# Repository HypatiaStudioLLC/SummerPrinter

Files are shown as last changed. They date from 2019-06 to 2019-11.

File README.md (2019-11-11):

# SummerPrinter

Here you will find information about our 3D printer design.  This 3D printer was developed for our Build Your Own 3D Printer summer camps, which we ran in the summer of 2019 in Boulder, Colorado, USA.  At present we have 3D model files for all the 3D printed components of the printer, basic documentation, a bill of materials, and firmware configurations for Marlin.  More information is to come, and updates to the design as we improve it!

Our goals for this printer are, in no particular order, that this printer should:
* Print quickly and with high quality (not necessarily at the same time)
* Be compact and portable
* Be able to be assembled and commissioned by a teenager -- under supervision -- in a week-long half-day summer camp
* Print the three common materials (PLA, PETG, ABS)
* Have low cost
* Use standard components as much as possible to enable expansion and experimentation

(One motivation behind these goals was that, if we turned out to not get sign-ups for the camp, I wanted printer kits that I would be happy to assemble and use myself in our other classes.  Thus we would need to carry these printers into classrooms or community centers and use them without much setup, and we would use them to quickly print small objects that students design during a workshop or class.)

These goals led to the following design decisions:
* The printer uses a cartesian (Makerbot-style) motion system.  A Prusa-style motion system has limited acceleration due to the need to move the build plate and print horizontally.  CoreXY and delta motion systems support fast printing, but both systems are harder to comprehend in terms of how motor movement translates to motion of the printhead.  CoreXY systems also tend to be more complex and have long, difficult-to-thread belt paths, and delta systems are sensitive to misalignments during assembly.
* To support quick printing the X gantry is driven by a small NEMA 14 stepper motor and uses 6 mm rods.  These are acceptable for a small printer with a light-weight printhead, but would not scale up well.
* The printer has a 160 x 160 x 160 mm print area in a frame with outer dimensions 300 x 340 x 343 mm.  The printable area puts the printer in the 'mini' size category, but it is at the larger end of that range.  The small build plate makes running a heated bed on 12 V practical, even at ABS temperatures.
* All moving parts of the printer are contained within the frame, except for the bowden tube running between the printhead and extruder.  Thus the printer can easily be semi-enclosed (front, back, sides, and bottom) for ABS printing by installing coroplast or other plastic panels on the outside of the frame.
* Despite the small size, the build plate is supported at both ends.  The build plate remains stable even when using z-hop during printing.
* The printer has a basic graphical display and SD card slot, so it can print without being tethered to a computer via USB or a network.
* The low-cost goal requires a number of compromises, of course, the most significant of which are the following:
  * The motion system uses smooth rods and linear bearings sourced from low-cost providers via Aliexpress -- thus they often do not meet their advertised specifications and have significant slop.  This is mitigated somewhat in the Y and Z axes with preload putting opposing side-load on the two linear bearings on each axis.  For better print quality the rods and bearings can easily be replaced with ones from reputable suppliers, such as Misumi, at increased cost.
  * The printer uses 8-bit electronics -- the old standard of an Arduino Mega, RAMPS, and A4988 or similar stepper drivers.  Due to the current draw of the heated bed a RAMPS 1.6 or 1.6+ is needed, or a heat sink could be added to the bed MOSFET of a RAMPS 1.4.  The printer can stall when printing detailed models from an SD card due to falling behind processing lines of G-code.  To avoid that problem the electronics can be upgraded to a 32-bit board, such as an SKR 1.3 or Smoothieboard, which also makes the graphical display more responsive.
  * Many quality-of-life features are not included in the design, such as any sort of automated bed levelling or a filament runout sensor.  It is envisioned that students may wish to add these features on their own after the conclusion of camp.

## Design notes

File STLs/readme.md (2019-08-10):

This directory contains .stl files needed to make the 3D printed components of the printer.

All files should print successfully without support.  Files are oriented in the best printing orientation, with positive Z being vertically up on the printer.  In general, parts associated with the motion system should be printed in ABS with four perimeters and generous infill.

ATX Mount* files are for mounting a desktop computer ATX power supply to the printer frame for the printer's power supply.
PS* files are for mounting a Meanwell 12V/29A power supply.  The tall bottom cover is for use with power inlets that use blade connectors that need a bit more space.
You only need to print one of these two sets of files, depending on your hardware.

Drill bushing holder.stl is tooling -- use it with 5mm ID drill bushings to cross-drill extrusion pieces at the correct locations if your extrusions are not already cross-drilled.
Z * spacer.stl files are also tooling, used to align the top and bottom anchors for the Z shaft such that the shaft is vertical.

Extruder mount.stl is needed only if you have an MK8-style extruder that did not come with a mounting bracket.
Mobius mount.stl can be used to mount a Voron Mobius 3 extruder vertically in the place of an MK8-style extruder.

Frame spacer.stl is needed only if you discover at the last minute that your Z-axis smooth rods are about 3mm longer than they should be and they don't fit in the frame!

Bed Standoff.stl is needed to mount the print bed only if you discover at the last moment that your mounting screws are significantly longer than the bed springs!

MKS* files are for mounting MKS-base electronics to the printer frame.
RAMPS* files are for mounting an Arduino Mega + RAMPS boards to the printer frame.
SKR 13* files are for mounting SKR 1.3 electronics to the printer frame.
You only need to print one of these three sets of files, depending on your hardware.

Panel clip.stl is optional, use several of these to attach coroplast sheets to the outside of your frame, if desired.

X carriage duct.stl may need to be printed with fewer perimeters than the other parts -- 2 perimeters or 0.8mm wall thickness -- to get the roof to print successfully.  Check the print preview in your slicer before printing and make sure the infill lines extend all the way to the walls on the first layer of the roof.

Cable Clip* files are used to secure the printer wiring in place.  Expect to use at least four of each size; having more won't hurt.  Be sure to print these in ABS; if printed in PLA the plastic will creep over time and become loose in the frame extrusions.

Foot.stl is optional, you can use any sort of rubber feet on the bottom of the printer instead.  If you use these printed feet, be sure to print them in ABS; if printed in PLA they will sag or crack over time.  It would be interesting to try printing them in TPU.

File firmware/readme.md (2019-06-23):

This directory contains firmware configuration files -- at present, there is only one that is set up for Marlin running on Arduino Mega + RAMPS + A4988 drivers.
To use configuration.h, first download and install the Arduino development environment (IDE) from https://www.arduino.cc/en/Main/Software .
Then, get version 1.1.9 of Marlin firmware from http://marlinfw.org/meta/download/ and unzip it into a directory on your computer.
Replace the configuration.h file in that download with the file from this directory, which is already configured for this printer's hardware.
If you'd like to alter anything in the firmware, start by reading Marlin's excellent documentation at http://marlinfw.org/docs/configuration/configuration.html .

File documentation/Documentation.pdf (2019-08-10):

Warnings (don’t hurt yourself!):
Power supply: As discussed in camp, do not remove the inside cover on the power supply – that’s where the 120V wiring is, and it’s an electrocution hazard. (Just like you shouldn’t open up the power supply of any other equipment!) If you ever need to connect additional 12V loads to the power supply, you can remove the cover underneath the socket to access the +12V and ground terminals. If you’re not totally comfortable doing that, get someone to help.

Hotend and bed: The hotend and bed are capable of reaching temperatures of at least 275 °C and 120 °C, respectively, which are burn hazards. You can’t tell that either one is hot just by looking at it, so always use caution – check the current temperature on the display or, if the printer is off, hold your hand near the part to check for heat before touching it.

Cautions (don’t hurt the printer!):
Heat-Hotend: Don’t turn off the printer immediately after finishing a print; let the hotend cool down to at least 120 °C first. If you turn off the printer while it’s still hot, the cooling fan on the hotend will stop and heat can leak from the heater block up into the parts of the hotend that are supposed to stay cool.

Heat-Bed: The Buildtak surface on your print bed says it can withstand a maximum temperature of 120 °C, but the heater on the bed is capable of getting hotter than that – so don’t try to push the bed to its limit. In general, try not to go hotter than 100 °C, even if printing high-temperature materials.

Electrical: Always turn off power to the printer before plugging or unplugging anything electrical. The stepper motor drivers are especially sensitive to this – unplugging a motor while it is powered is a good way to burn out its driver. Make sure you plug in connectors the right way around; some connectors, like for the endstops, can be plugged in either way around on the RAMPS board and getting it backwards can damage the electronics.

Mechanical: If you notice any belts slipping or if the X-gantry or bed assembly seem to be getting crooked, STOP! And figure out what is going on. This is most important on the Z axis – if one of the leadscrews stops while the other one keeps turning, the motor can exert enough force to break or bend part of that assembly.

More information:
We have uploaded the .stl files for the printer parts and firmware configuration files to https://github.com/HypatiaStudioLLC/SummerPrinter ; more information will be added there as quickly as I am able.

If you have questions about the printer or problems with it, please create an issue in the issue tracker there to discuss it. That way, others will also be able to join the conversation and learn from it.

Operating the printer:
Filament: You need filament to print with. If you’re new to printing, start with regular PLA from a good brand – we mostly use Hatchbox and it is almost always trouble-free. Esun also works well, in my experience. Don’t go to more difficult materials (PETG, ABS, etc.) or filled materials (wood-fill, metal-fill, etc.) until you have some printing experience.
It is possible to get a bad spool of filament from any brand, though it becomes more likely with especially cheap filament. Bad PLA will jam or underextrude repeatedly – if you just can’t get good prints, it might be the filament’s fault, not the printer; try a new spool.
For ABS, we have had good experiences with eSun’s ABS+ filament. (That’s what most of the printed parts in your printer were printed with.) It is best to print ABS in a well-ventilated location. Cheap ABS tends to have a stronger smell, but the fumes aren’t healthy to breathe in any case.
We don’t have enough experience printing PETG or other materials to recommend specific brands.

Printing pipeline: The general 3D printing pipeline is to create a design with 3D modeling software or a 3D scanner; export it as an .stl file (triangle mesh); use a slicer to convert the mesh to instructions for the printer (G-code); and send the G-code to the printer to print. Different software is used for each step.
3D modeling: Consider Tinkercad, Fusion360, Meshmixer, OpenSCAD, DesignSpark Mechanical, or BeetleBlocks. Other software options (that we have less experience with / do not like as much) include Vectary, FreeCAD, Blender, and Sketchup.
3D models: The most well-known site for downloading .stl files is thingiverse.com .
Slicing: We mostly use Cura 3.6; Repetier also works.
Printing: You can either connect your computer directly to the printer with a USB cable and have the slicer feed lines of G-code one-at-a-time during the print, or save the G-code file to an SD Card and insert it into the card slot in the display of your printer. The latter option is usually more reliable; you won’t have a print fail if your computer goes to sleep or installs updates in the middle of a print. The printer can be picky about cards; you might find that some work in your computer but not the printer.

Slicer settings: Slicers have dozens, if not hundreds, of settings that influence how they translate meshes into printer instructions. Here are some basic settings to start from; you will have to experiment to get the best performance from your printer!
When initially setting up Cura you can set basic parameters of your printer:

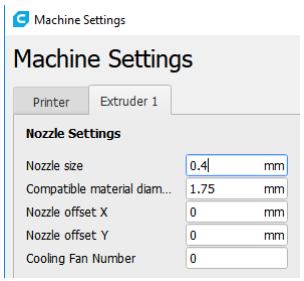
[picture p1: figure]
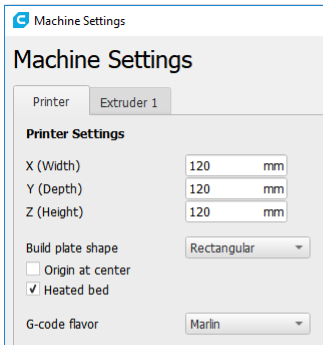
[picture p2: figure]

Dimensions: The print volume is rectangular with 160 mm size in x, y, and z. (Note that you will have to avoid the screw holes in the print bed if you want to use the full width of the bed.)
The bed is heated.
Filament diameter is 1.75 mm. (Watch out! Cura defaults to 2.85 mm.)

Temperatures: Nozzle and bed temperatures depend on the material and brand; start with the brand’s recommended temperatures – usually PLA is around 200 °C for the nozzle and 50 °C for the bed. Layer height: Start with 0.2mm layers; we have printed jewelry successfully at 0.05mm layer height. Use layer heights that are multiples of 0.01mm.
Print speed: We normally use 80mm/s with 50mm/s outer perimeter speed and 200mm/s travel; Cura’s defaults are a bit slower.
Cooling: For PLA, enable cooling with the fan speed at 75% or more. For ABS, use 35% fan speed. Retraction: Enable retraction, with a retraction distance of 2mm. Retraction speed can be increased to 50mm/s or so. Cura defaults to 6.5mm retraction distance, which is way too high.
Bed adhesion: If you have your bed leveling and first layer spacing dialed in well, you should usually not need any bed adhesion. If you are printing a model with a small base or that mostly has support material touching the bed, you might wish to enable a small brim to help the support material stay put.

About the printer:
Hardware: This printer is based on a frame made of 2020 aluminum extrusions, which is pretty standard for printer kits and, for a printer this size, makes for a very rigid frame. In general, any accessories that are made to be mounted to 2020 or ‘v-slot’ extrusion will fit on this printer frame. The motion system is designed to fit entirely inside the frame so that you can place panels on the sides and bottom to partially enclose the printer.

The motion system is Makerbot-style, in which the hotend moves on a gantry in the X direction (sideto-side), and the whole gantry, including X-axis motor, moves in the Y direction (front-to-back). The bed itself moves in the Z direction (up-and-down). The speed of this style of printer can be limited by the need to sling the weight of the X-axis gantry around, but in this design we took care to keep the mass of that assembly low, so high print speeds and accelerations are possible.

[Aside: Low-cost printers more commonly use a Prusa-style motion system, in which the bed moves in the Y direction, but it is difficult to print at high speed and quality with such an arrangement. (Genuine Prusas do very well, but they are not low-cost!) Other common motion systems include CoreXY (fast, but pretty complex) and Delta (fast, but prone to subtly distorting prints if the geometry is not exactly right).]

The bed is supported by leadscrews on both sides of the printer, which prevents vibration from movement of the printhead from translating into shaking of the bed.

The hotend (where the plastic gets melted with the nozzle) is a clone of the all-metal E3D V6 hotend made by Trianglelab. The E3D documentation at https://e3d-online.dozuki.com/c/V6 applies to this hotend as well. Any nozzles that fit an E3D V6 hotend should fit this hotend.

The extruder is a clone Mk 8 extruder.

The print bed is 160mm x 160mm and has an integrated 12V heater. The printing surface is genuine Buildtak, which provides very good adhesion for PLA prints. You can find troubleshooting and maintenance information for Buildtak at https://www.buildtak.com/support/#FAQ .

The stepper motors are 1.8° per step (200 steps per revolution); the Y, Z, and extruder steppers are rated for 1.5A max and the X stepper is rated for 1.0A max. Don’t run the steppers at more than about 2/3 of their rated current; they will get hot enough to soften the 3D printed parts they are attached to.

Electrical: The power supply is a Meanwell 12V power supply rated at 29A; the printer should draw around 17A max, so there is room to grow or add accessories. The control electronics consist of an Arduino Mega board with a RAMPS V1.6+ board on top of it and A4988 stepper motor drivers. If you should ever wish to use these electronics in a larger printer with a more demanding heatbed, you can attach the bar-shaped heatsink to the power transistors on the RAMPS board to make sure they can handle the higher current without overheating; the heatsink is not needed for this printer. (See https://reprap.org/wiki/RAMPS_1.6 .) The labels on the screw terminals on the RAMPS board are rather mysterious; D10 is for the hotend heater, D9 is for the print cooling fan, D8 is for the bed heater, and the terminals below them are for power input. The display is a RepRapDiscount Full Graphic Smart Controller. The Arduino is running Marlin firmware version 1.1.9.

Maintenance:
Electrical: Periodically check the large wires that connect to the screw terminals through the bottom of the electronics case – they can work loose over time. Just give gentle tug on each wire and, if it budges, tighten down the screw for that terminal.

Mechanical: We greased the leadscrews for the Z axis with synthetic grease (Super Lube with PTFE), they may require additional grease over time if they start making noise. Use the same type of grease; don’t use oil.

The bearings, both linear and rotational, are lubricated at the factory and should not need additional lubrication.

The hotend cooling fan will eventually go bad; the bearings on these small fans just wear out over time. If it doesn’t spin freely or starts to make noise, it is time to replace the fan. For replacements, look for an E3D V6 hotend fan. (If the replacement fan comes with long-enough wires, you might wish to wire it directly to the 12V terminals on the power supply rather than the control electronics.) The partcooling blower (on the back of the printhead) should last a long time.

Heatbed: The Buildtak surface should last a long time for PLA. The surface may get dirty or oily over time; you can clean it with isopropyl alcohol (rubbing alcohol). Don’t use acetone or other harsh cleaning agents. If cleaning the Buildtak doesn’t restore its stickiness, you can also try lightly sanding the surface with medium-grit sandpaper. At ABS temperatures (100 °C or more), the surface will have limited life, mostly due to the adhesive under it wearing out. To increase its life with ABS, run the bed at the lowest temperature that gives adequate adhesion, which will probably be around 90-100 °C. There’s a good recent video by Maker’s Muse on Youtube that discusses how to clean print beds here: https://www.youtube.com/watch?v=ShFaJ027pFs .

Expect to have to adjust the bed’s height periodically, using the screw on the Z endstop, especially if you move the printer or change materials. You shouldn’t have to go through the full leveling procedure again. If you find that prints don’t stick well on one end of the bed, that may indicate that you have to raise that end of the bed slightly. Look at the amount of ‘squish’ the first layer of prints has and see if it is different in different areas.

Troubleshooting:

General print troubleshooting: There is an overall troubleshooting guide for printing problems on the reprap website here: https://www.reprap.org/wiki/Print_Troubleshooting_Pictorial_Guide . Another good guide can be found by MatterHackers here: https://www.matterhackers.com/articles/3d-printertroubleshooting-guide (https://www.matterhackers.com/articles/3d-printer-troubleshooting-guide) . Finally, Simplify3D has one as well, although some of it is specific to their slicing software, here: https://www.simplify3d.com/support/print-quality-troubleshooting/ . It is good to peruse these, just to get an idea of what can go wrong in a print and what to watch out for.

Here are some troubleshooting tips specific to this printer.
Consistent under-extrusion: If the printer seems to operate correctly but the print is uniformly underextruded throughout the entire print, first check your printer settings in Cura – make sure that the printer configuration has the filament diameter set to 1.75 mm instead of 2.85. Find the printer settings in Cura preferences in the printers category, then click on the ‘machine settings’ button while your printer is selected. If/whenever you upgrade Cura you should check this parameter again; Cura likes to reset it to 2.85mm.

Occasional jamming/under-extrusion: If the extruder jams periodically – you hear or see the extruder motor skipping – there are a few possible causes.
- Make sure the hotend cooling fan is running; if the upper portion of the hotend gets warm it can lead to jams (heat creep).
- Make sure the retraction distance in Cura is not excessive – around 2mm is usually best, but Cura defaults to 6.5mm. Excessive retraction pulls hot plastic up into the cool part of the hotend, where it can freeze and jam.
- Old PLA filament, or low-quality PLA filament, is prone to jamming. PLA picks up moisture from the atmosphere over time, and as it gets more problematic. In our dry Colorado climate you can expect PLA to last at least six months after it comes out of its packaging; if you want a roll to last a year or more you should store it in a sealed bag or box with dessicant.
- If the extruder motor is cold or cool to the touch even after running a print, you can adjust the motor’s current higher, which will allow it to push the filament harder. It is difficult to describe how to adjust the motor current in writing – look for tutorials on adjusting A4988 driver current online. For these boards, the motor current will be 1.25 times the voltage measured between ground and the potentiometer on the driver board. Make small adjustments and check the motor temperature after a print before increasing current further; it is fine if the motor gets warm to the touch but it should not get uncomfortably hot.

Layer shifts: This printer is somewhat more susceptible to layer shifts in the X direction if the printhead catches on something due to the smaller-than-usual X axis motor. If possible, orient your prints such that any steep overhangs run in the Y direction. You can also enable Z hop in Cura for difficult cases; only 0.5mm or so of hop should be needed.

Occasional printing slowdowns/pauses: If you print files with many small triangles, you might find the printer occasionally slowing down or pausing while printing. This is caused by the controller being unable to process lines of G-code fast enough. (Each triangle in a layer translates to one line segment and one line of G-code.) Possible cures include:
- Increase the maximum resolution setting in Cura (default is 0.01mm, try going to 0.03mm); that will force Cura to combine very short moves and reduce the number of lines of G-code.
- Slowing down the printing speed helps the controller keep up.
- Use a program such as Meshmixer or Meshlab to reduce the number of triangles in the .stl file.
- Upgrade the printer’s controller to one with more processing power. You can add a Raspberry Pi to the existing controller and run Klipper firmware; or replace the Arduino board with a Re-

ARM board (while keeping the RAMPS board); or replace the controller electronics altogether with a Smoothieboard, MKS-Sbase, SKR 1.3 motherboard, Duet, etc.

Upgrading/going further:
Now that you have your own 3D printer, you will probably find that you want to do more than you can with this printer. The following are some suggestions for various improvements/applications:

I want to print high-temperature materials (ABS, Nylon, etc.): Your printer can print ABS+ without any modification. You will get better results from adding side and bottom panels to the printer to eliminate drafts. If you plan to print lots of ABS, consider replacing the Buildtak bed surface with PEI, which will stand up to ABS temperatures for longer. Higher-temperature materials than ABS may require a full enclosure, which may in turn require an upgraded hotend cooling fan to prevent jams.

I want to print filled PLA (glow-in-the-dark, metal-fill, wood-fill, carbon fiber-fill, etc.): These materials are abrasive and will wear away a standard brass hotend nozzle over time. If you plan to print a lot of these materials you should have a spare nozzle on-hand, and you may want to consider getting a steel or other hardened nozzle.

I want to print large things faster: The standard Cura settings come nowhere near maxing out the speed of this printer. You should be able to reach 100mm/s print speeds or more, but expect to have to adjust your hotend temperature upwards somewhat and adjust other settings as well – this takes experimentation. You might also want to consider getting a nozzle with a larger opening, such as 0.8mm. Larger nozzles allow you to extrude plastic more quickly, but will reduce the detail in your finished prints. See E3D’s V6 documentation to see how to replace nozzles.

I want to print small, detailed models (miniatures, etc.): You might want to consider installing a smaller nozzle, such as 0.25 or 0.3mm, to allow the printer to print finer details. Printing thinner layers also leads to smoother, more detailed prints. Choose layer heights that are multiples of 0.01mm, as that is the distance the bed moves from a single full step of the Z motor. You might also consider switching to a geared extruder or a 0.9 degree stepper motor for the extruder, as either change will allow the extruder to push small amounts of plastic more precisely. For geared extruders, I personally prefer the Voron Mobius extruder, but that is a fairly complex build.

I want to print larger models than fit on this printer: You can use Meshmixer or Blender to cut models into parts, print them separately, and glue the parts together. Or, you need a larger printer! You can use this printer to print parts for a second printer – consider a Voron, RailCore, or Hypercube Evolution (NOT the original Hypercube); all are considered to be good. Or you may wish to purchase a new printer. I don’t have much advice there, except to avoid Anet A8s (they are fire hazards).

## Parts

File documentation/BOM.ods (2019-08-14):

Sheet: Hardware
Summer Camp 3D printer V 1.01 BOM
Part description | P/N | Quantity | Source | Comments
Structure, tools
2020 Extrusion 300mm lg, plain | HFS5-2020-300 | 2 | Misumi | Plain extrusions for Z carriage
2020 Extrusion 300mm lg, crossdrilled | HFS5-2020-300-LCP-RCP | 4 | Misumi | Extrusions with wrench holes for frame in Y-direction
2020 Extrusion 300mm lg, ends tapped | HFS5-2020-300-TPW | 4 | Misumi | Extrusions with ends tapped for frame in X-direction
2020 Extrusion 304mm lg, ends tapped | HFS5-3030-304-TPW | 4 | Misumi | Extrusions with ends tapped for frame in Z-direction
Notes on frame: This design was intended to use all 300mm-long extrusions, but the Z-axis rods must fit between the Z-axis frame extrusions. It turns out our supplier provided Z rods 2-3mm longer than the requested 300mm, so we use slightly longer 304mm-long extrusions for the Z axis of the frame to compensate. The provided part numbers are for extrusions with the tapped and drilled holes necessary to assemble the frame. If you prefer, you can tap and drill the extrusions yourself and save about $48 on the price of the extrusions. To go this route, order plain extrusions (omit the -LCP -RCP and -TPW suffixes on the part numbers). A tap with spiral flutes is strongly recommended, e.g. McMaster-Carr part number 26475A38. To drill the wrench holes in the proper locations, print the drill jig part found in the .stls folder and insert two 5mm drill bushings, e.g. McMaster-Carr part number 8486A424, and use with a 5mm drill bit.
Motion
8x300 mm smooth rod |  | 4 | CNA Mech. Parts Store | Y and Z axes; this supplier is on Aliexpress
6x250 mm smooth rod |  | 3 | CNA Mech. Parts Store | X axis and x-axis axle, the two x-axis rods should be g6 tolerance
LM8LUU long linear bearing |  | 4 | CNA Mech. Parts Store | Y and Z axes
LM6LUU long linear bearing |  | 2 | CNA Mech. Parts Store | X carriage
GT2-16 pulley, 5mm shaft |  | 2 | Powge | X and Y steppers; this supplier is on Aliexpress
GT2-16 idler, 3mm shaft |  | 3 | Powge | X and Y belts
GT2-20 pulley, 6mm shaft |  | 5 | Powge | Y and Z belts
GT2-20 pulley, 5mm shaft |  | 1 | Powge | Z stepper motor
NEMA14 stepper | 14HS11-1004S | 1 | OMC Stepper Online | X axis
NEMA17 stepper | 17HS15-1504S1 | 3 | OMC Stepper Online | Y and Z axes, extruder
F686-RS flange bearing |  | 4 | Fushi | Y and Z axes; this supplier is on Aliexpress; F686-ZZ bearings also OK
6x250 mm leadscrew, 2mm pitch |  | 2 | LinkCNC | Z axis; this supplier is on Aliexpress
6mm leadscrew nut, 2mm pitch |  | 2 | LinkCNC | Z axis
GT2 550x6 mm belt |  | 2 | Powge | Y axis; Belts from Powge are genuine Gates belts
GT2 98x6 mm belt |  | 1 | Powge | Y axis
GT2 696x6 mm belt |  | 1 | Powge | Z axis
700mm of open GT2 6mm belt |  | 1 | Powge | X axis; can also use a spare Z axis belt and cut to length
Electronics / Printing parts
Heatbed, 160x160mm |  | 1 | https://www.aliexpress.com/item/32857294742.html; get 160x160mm option
E3D V6 clone hotend |  | 1 | Trianglelab | This supplier is on Aliexpress; can also get genuine E3D hotend
45 x 45 x 15 mm blower | BM4515-04W-B50-L00 | 1 | NMB | Part cooling fan for X carriage; try Aliexpress or Digikey
Heatbed surface |  | 1 | Buildtak | Available on Amazon, will have to cut sheets to fit
Arduino+RAMPS+drivers+display |  | 1 | Bigtreetech | This supplier is on Aliexpress; get whatever set of electronics you prefer
Meanwell Power supply | LRS-350-12 | 1 | Meanwell | Arrow electronics usually has the best price on Meanwell power supplies
Endstop switches |  | 3 | Bigtreetech
Stepper connector | WM2802-ND | 1 | Digikey | The x-axis stepper comes without a connector
Stepper connector pins | WM2562CT-ND | 4 | Digikey | Will need a crimping tool – PA09 is recommended
Extruder
Extruder |  | 1 | LinkCNC | All-in-one! – make sure the extruder kit includes a mounting bracket
Bowden tube |  | 1 | Trianglelab
Fasteners
2020 T-slot nut 5mm |  | 22 | Misumi
2020 T-slot nut 3mm |  | 20 | Misumi
locknut 4mm |  | 2
locknut 3mm |  | 14
nut 3mm |  | 3
Flat washer 3mm |  | 2
2.5x6mm SHCS |  | 6
3x6mm screw |  | 15 |  | Socket head preferred
3x8mm screw |  | 13 |  | Socket head preferred
3x10mm SHCS |  | 19 |  | Socket head required in two places
3x12mm screw |  | 8 |  | Socket head preferred
3x16mm SHCS |  | 7 |  | Socket head required in two places
3x20mm SHCS |  | 5 |  | Socket head required in three places
3x20mm BHCS |  | 4 |  | Button head required
4x6mm screw |  | 4 |  | Button head or socket head OK
4x12mm screw |  | 2 |  | Button head preferred
5x14mm BHCS |  | 17 |  | Button head required in 16 places
5x10mm BHCS |  | 21 |  | Button head required in 2 places
2.5x8mm wood screw |  | 6
Other Hardware
Springs |  | 4
Power inlet |  | 1

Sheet: Printed Parts
Part | Qty | Material
X Carriage Body | 1 | ABS
X Carriage Duct | 1 | ABS – thinner walls
X Carriage Hotend Clamp | 1 | ABS
XY Joiner Left | 1 | ABS
XY Joiner Right | 1 | ABS
X Belt Idler | 1 | ABS
Y Belt Clamp | 2 | ABS
Y Anchor Front Left | 1 | ABS
Y Anchor Front Right | 1 | ABS
Y Anchor Back Left | 1 | ABS
Y Anchor Back Right | 1 | ABS
Y Endstop Mount | 1 | ABS
Y Motor Mount | 1 | ABS
Z Bearing Block Top | 2 | ABS
Z Bearing Block Bottom | 2 | ABS
Z Endswitch Holder | 1 | ABS
Z Base Left | 1 | ABS
Z Base Right | 1 | ABS
Z Shaft Anchor | 2 | ABS
Z Endstop | 1 | ABS
Z Motor Mount | 1 | ABS
Bed standoff | 4 | ABS | (Only if needed with short springs and long bed screws)
PS Case | 1 | ABS/PETG
PS Top Cover | 1 | Any
PS Bottom Cover | 1 | Any
PS Bracket | 1 | ABS/PETG
Display Case Front | 1 | Any
Display Case Back | 1 | Any
Display Case Hinge Base | 2 | ABS
Display Case Hinge | 1 | ABS
RAMPS Case Base | 1 | Any | (Or other electronics enclosure)
RAMPS Case Lid | 1 | Any | (Or other electronics enclosure)
Foot | 4 | ABS | (Only if needed)
Cable Clamp small | 4 | ABS | (or more, as needed)
Cable clamp large | 4 | ABS | (or more, as needed)
Filament hook | 1 | Any

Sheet: Fasteners
Hardware | Qty | Use
Frame
5x14 BHCS | 16 | Frame
X Carriage
3x20 screw | 2 | Hotend clamp
3mm nut | 2 | Hotend clamp
3x16 screw | 2 | Print cooler blower
3x8 screw | 1 | Print cooler duct
3mm nut | 1 | Print cooler duct
3x10 SHCS | 2 | X belt ends
XY Joiners
3x12 screw | 4 | Y belt clips
3mm locknut | 4 | Y belt clips
3x20 SHCS | 1 | X belt idler
3mm locknut | 2 | X belt idler
3x16 SHCS | 1 | X belt idler
3x8 screw | 4 | X stepper motor
2mm wood screw | 2 | X endstop switch
Y Anchors
3x20 SHCS | 2 | Y belt idlers
5x10 BHCS | 8 | Y anchors
5mm T-slot nut | 8 | Y anchors
Y Motor Assembly
3x10 screw | 4 | Y stepper motor
5x10 BHCS | 2 | Y stepper motor mount
5mm T-slot nut | 2 | Y stepper motor mount
Y Endstop Mount
2mm wood screw | 2 | Y endstop switch
3x10 screw | 1 | Y endstop holder
3mm T-slot nut | 1 | Y endstop holder
Bed Assembly
3x20 BHCS | 4 | Bed anchors – maybe 3x16 BHCS if bed springs are short
3mm T-slot nut | 4 | Bed anchor screws
5x10 BHCS | 3 | Z bearing blocks
5x14 BHCS | 1 | Z bearing block & Z endstop switch holder
5mm T-slot nut | 4 | Z bearing block
2mm wood screw | 2 | Z endstop switch
3x12 screw | 4 | leadscrew nuts
3mm locknut | 4 | leadscrew nuts
Z Axis Assembly
3x10 screw | 4 | Z axis top anchors
3mm T-slot nut | 4 | Z axis top anchors
3x10 screw | 4 | Z axis bottom anchors
5x10 BHCS | 2 | Z axis bottom anchors
3mm T-slot nut | 4 | Z axis bottom anchors
5mm T-slot nut | 2 | Z axis bottom anchors
3x10 screw | 1 | Z axis endstop
3mm locknut | 1 | Z axis endstop
3x16 SHCS | 1 | Z axis endstop
3x8 screw | 4 | Z stepper motor
5x10 BHCS | 2 | Z stepper motor mount
5mm T-slot nut | 2 | Z stepper motor mount
Power Supply Assembly
5x10 BHCS | 3 | Power supply mount
5mm T-slot nut | 3 | Power supply mount
3x6 screw | 4 | Power supply covers
4x6 screw | 4 | Power supply
Display Assembly
3x8 screw | 2 | Display mount
3mm T-slot nut | 2 | Display mount
4x12 screw | 2 | Display hinge
4mm locknut | 2 | Display hinge
3x6 screw | 4 | Display hinge bases
3x6 screw | 3 | Display lid
3x16 screw | 3 | Display (display has four screw holes, but they tend to be misaligned a bit – probably only three screws will fit)
3mm locknut | 3 | Display
RAMPS Electronics Assembly
2.5x6 SHCS | 6 | Arduino
3x6 screw | 4 | Case lid
3x10 screw | 3 | Case to frame
3mm T-slot nut | 3 | Case to frame
Others
3x8 screw | 2 | Extruder to frame
3mm washer | 2 | Extruder to frame
3mm T-slot nut | 2 | Extruder to frame
5x10 BHCS | 1 | Filament hook
5mm T-slot nut | 1 | Filament hook

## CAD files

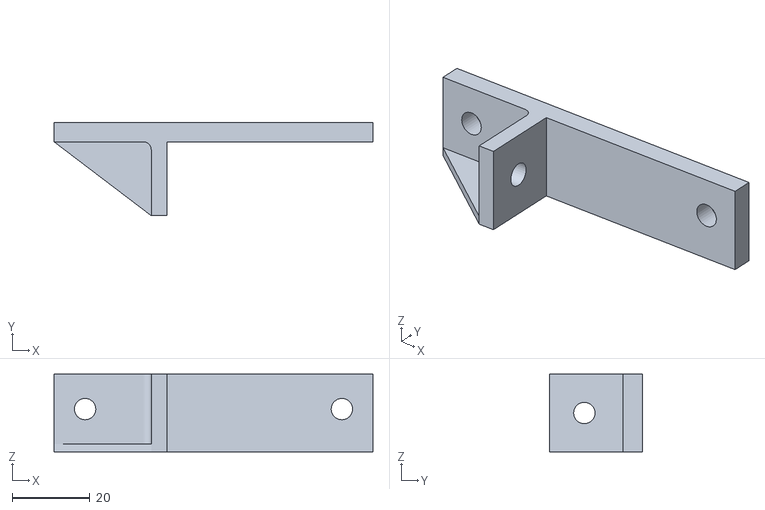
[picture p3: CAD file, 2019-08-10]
STLs/Mobius mount.stl
82.0 x 24.0 x 20.0

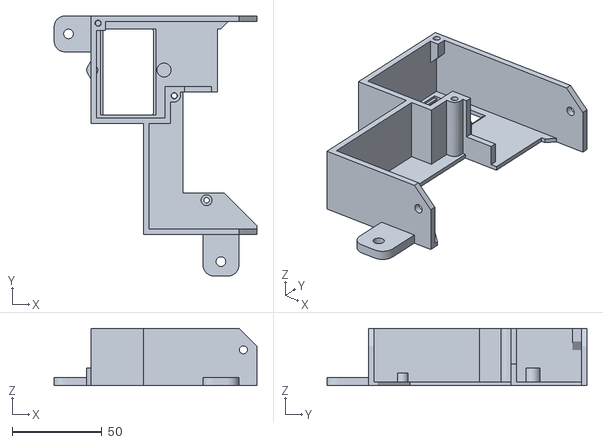
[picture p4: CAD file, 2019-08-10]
STLs/PS Case.stl
112.9 x 144.8 x 32.0

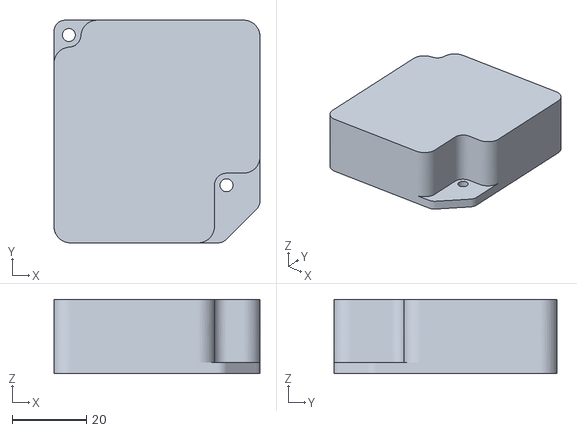
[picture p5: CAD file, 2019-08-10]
STLs/PS Case tall bottom cover.stl
55.4 x 59.9 x 20.0

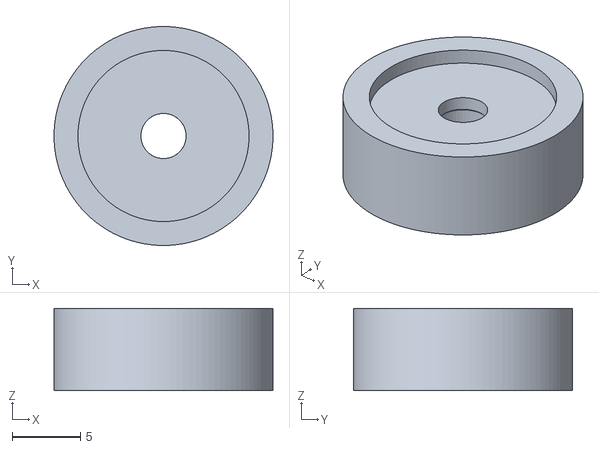
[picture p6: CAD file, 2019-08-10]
STLs/Bed Standoff.stl
16.0 x 16.0 x 6.00

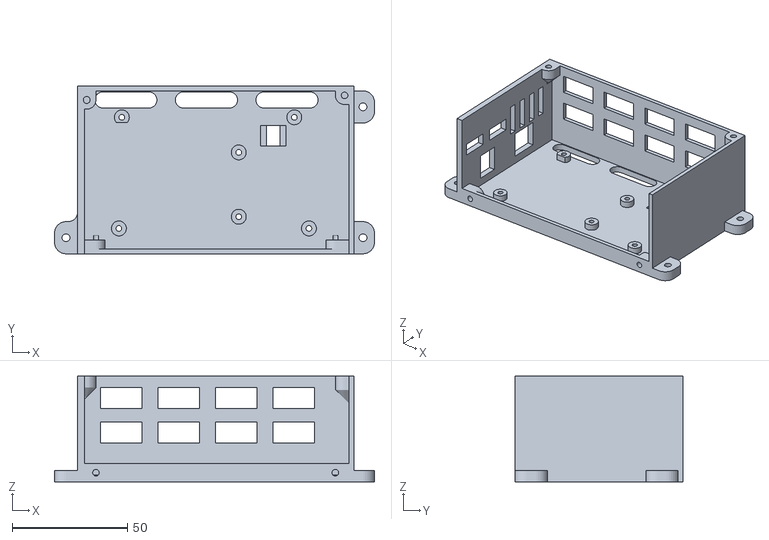
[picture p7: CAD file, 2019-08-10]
STLs/RAMPS base and sides.stl
139.0 x 72.8 x 46.0

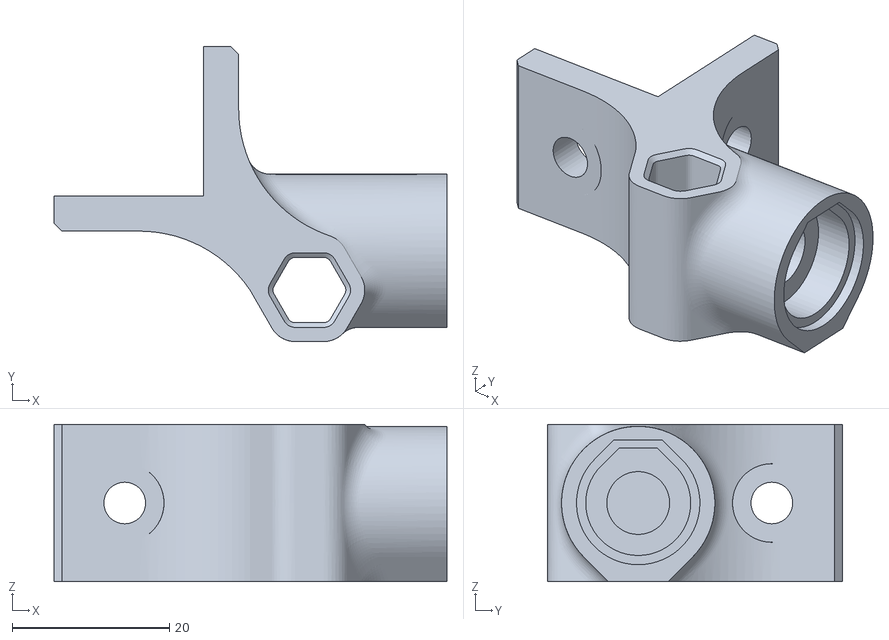
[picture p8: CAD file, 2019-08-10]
STLs/Y anchor back left.stl
50.0 x 37.6 x 20.0

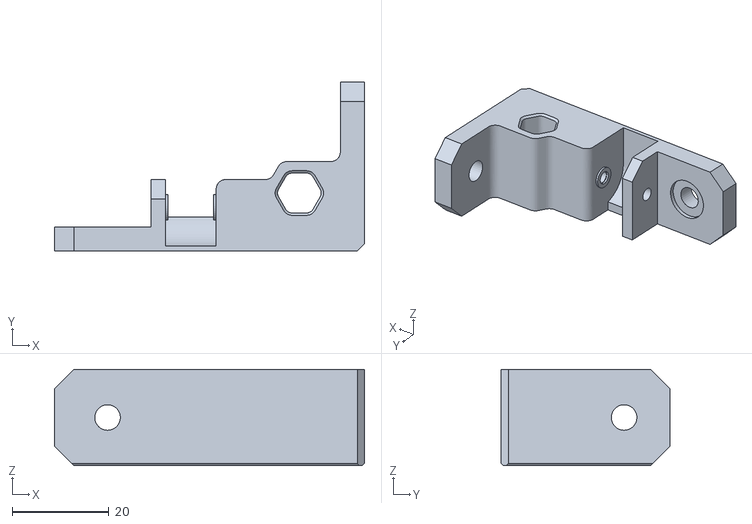
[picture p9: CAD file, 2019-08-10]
STLs/Y anchor front right.stl
64.2 x 35.0 x 20.0

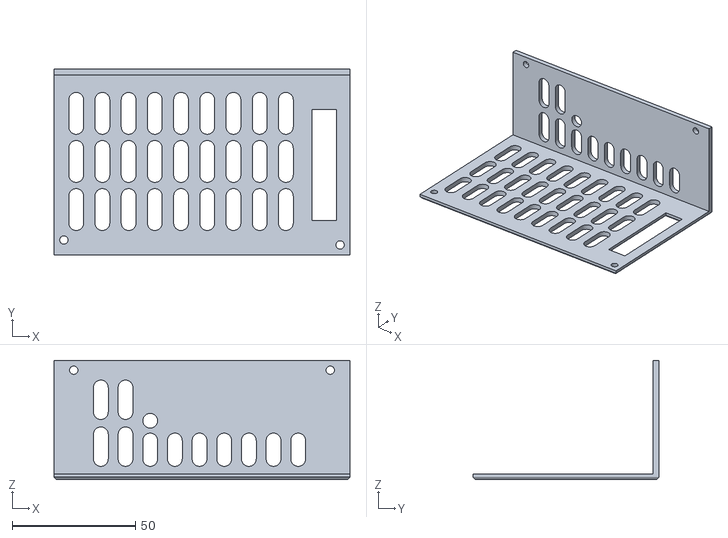
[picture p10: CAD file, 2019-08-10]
STLs/RAMPS Lid.stl
120.0 x 75.2 x 48.4

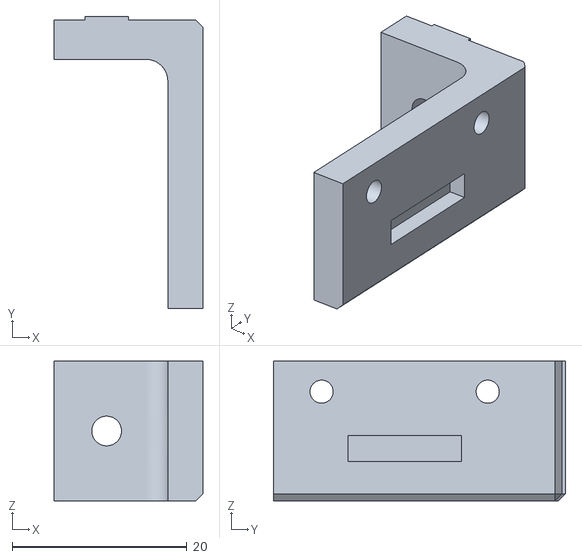
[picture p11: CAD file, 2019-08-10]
STLs/Y Endstop Holder.stl
17.0 x 33.4 x 16.0

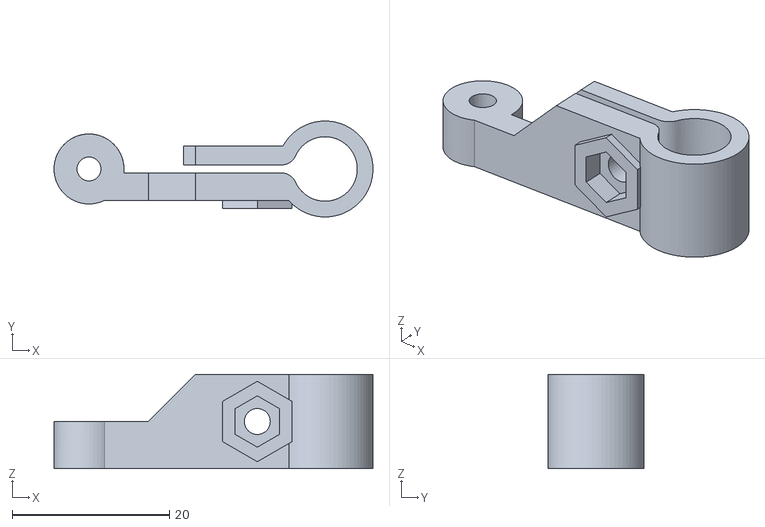
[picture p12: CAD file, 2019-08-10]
STLs/Z Endstop.stl
40.5 x 12.2 x 12.0

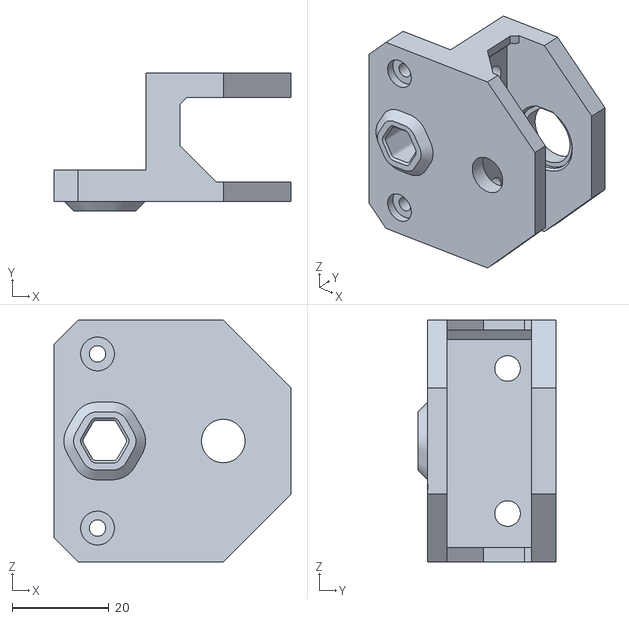
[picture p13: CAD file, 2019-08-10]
STLs/Z shaft base.stl
49.0 x 28.5 x 50.0

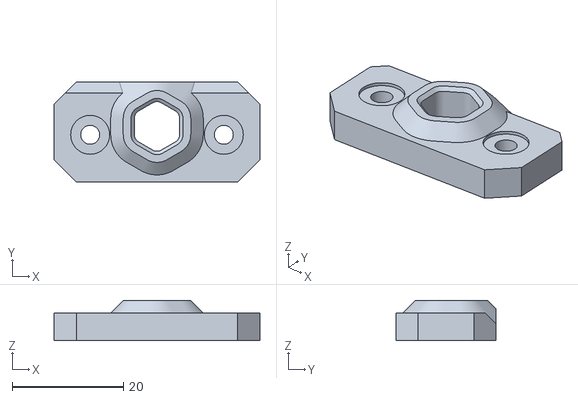
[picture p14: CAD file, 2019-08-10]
STLs/Z shaft top anchor.stl
37.0 x 18.0 x 7.25

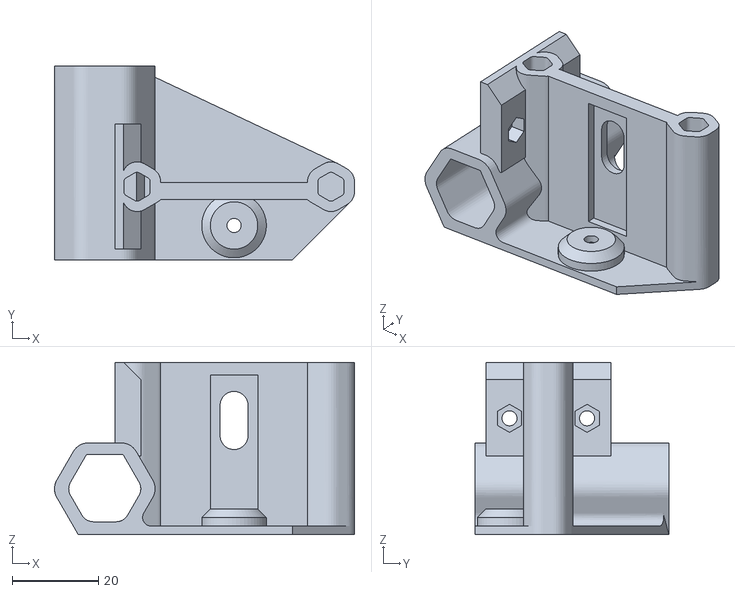
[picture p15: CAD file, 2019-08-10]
STLs/XY joiner right.stl
69.6 x 45.0 x 40.0

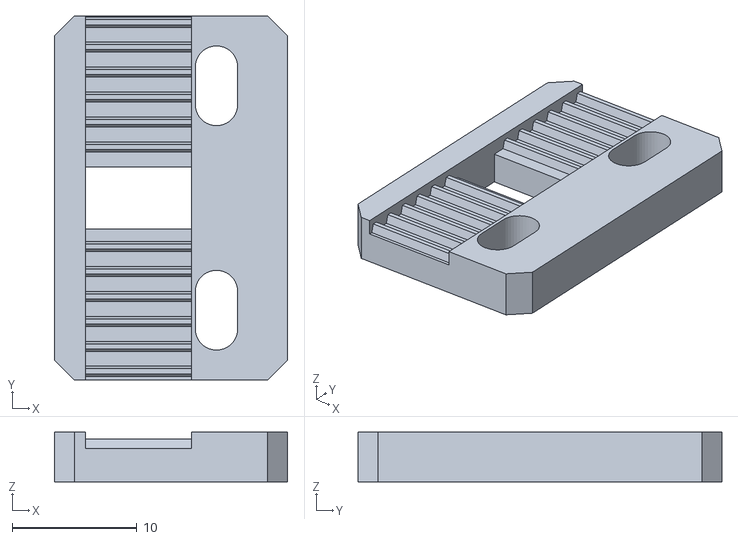
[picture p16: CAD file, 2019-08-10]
STLs/Y belt clip-hole.stl
18.7 x 29.2 x 4.00

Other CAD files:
STLs/Y anchor back right.stl
STLs/Y anchor front left.stl
STLs/XY joiner left.stl
STLs/X Carriage.stl
STLs/ATX Mount 1.stl
STLs/ATX Mount 2.stl
STLs/ATX Mount 3.stl
STLs/Cable Clip-11mm.stl
STLs/Cable Clip-7mm.stl
STLs/Display Base.stl
STLs/Display Hinge Base.stl
STLs/Display Hinge Bracket.stl
STLs/Display Lid.stl
STLs/Drill Bushing Holder.stl
STLs/Extruder mount.stl
STLs/Foot.stl
STLs/Frame Spacer.stl
STLs/MKS Base.stl
STLs/MKS Lid.stl
STLs/PS Bracket.stl
STLs/PS Case bottom cover.stl
STLs/PS Case top cover.stl
STLs/Panel Clip.stl
STLs/SKR 13 Base.stl
STLs/SKR 13 Lid.stl
STLs/Spool hook.stl
STLs/X belt anchor.stl
STLs/X carriage duct.stl
STLs/X carriage hotend clamp.stl
STLs/Y motor mount.stl
STLs/Z Bearing Block-Bottom.stl
STLs/Z Bearing Block-Top.stl
STLs/Z Endswitch Holder.stl
STLs/Z anchor spacer.stl
STLs/Z base spacer.stl
STLs/Z motor mount.stl

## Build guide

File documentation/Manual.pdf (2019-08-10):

Some general notes:

This printer is assembled almost entirely with metric hardware, either 3mm or 5mm diameter.

Generally you will use cap screws in one of two head styles – button head or socket head. In most cases either head style will work; when a particular one is required the screw will be denoted as SHCS (Socket Head Cap Screw) or BHCS (Button Head Cap Screw).

Nuts may be plain hex nuts or locknuts, which have a small plastic insert in one end that keeps any screw from vibrating loose over time. When using locknuts, install them so that when a screw is inserted into them, the screw engages the metal side first.

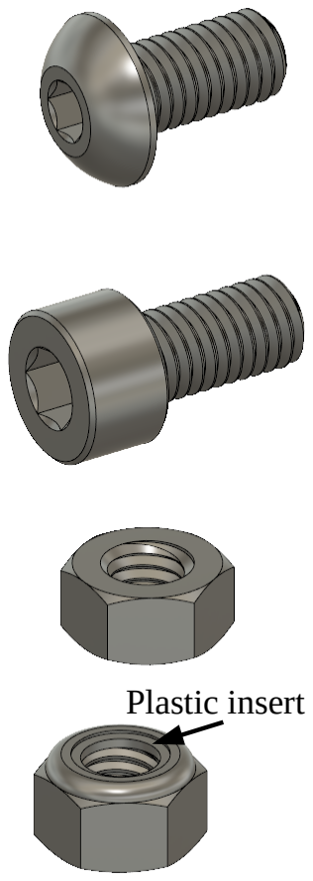
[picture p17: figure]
Plastic insert

In most cases, screws are used to clamp one or more plastic parts together and thread into metal (a nut of one sort or another). These screws should be tightened until snug – don’t leave them loose (except temporarily when instructed to do so), and don’t tighten them with all your strength; if you do so you can crush or crack the plastic parts.

In a few cases, when a screw doesn’t carry much axial load and shouldn’t have to be unscrewed again, the screw threads directly into plastic. Be gentle with these screws, tighten them just enough to keep the clamped parts from moving around. If you overtighten them you will strip the threads in the plastic.

When you are assembling the frame extrusions together, go ahead and tighten the screws down hard – the aluminum extrusions can take more load, and you don’t want them to shift.

Button Head Cap
Screw (BHCS)

Socket Head Cap
Screw (SHCS)

Plain hex nut

Locknut

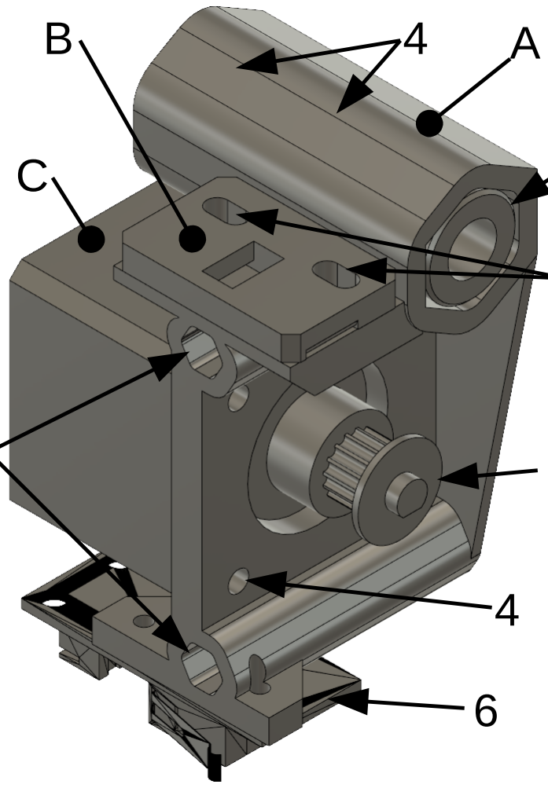
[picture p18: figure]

### Left XY Joiner assembly

32

1
5

1: Run 6mm drill through x-rod holes in body (A) to ensure rods will fit.
2: Insert long 8mm linear bearing into body.
3: Use 2x 3x12mm screws and 2x 3mm locknuts to secure y-belt clip (B) to body. Don’t tighten down screws yet.
4: Use 4x 3x10mm screws to secure x stepper motor (C) to body.
5: Install 14-tooth pulley on stepper motor. 6: Use 2x 2x8mm wood screws to secure x-axis endstop to body.

### Right XY Joiner assembly

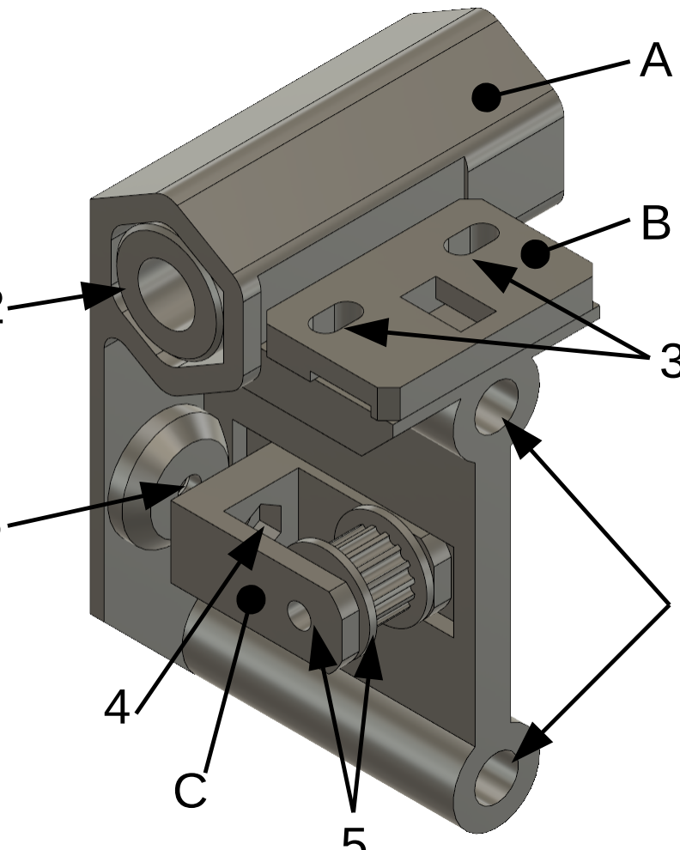
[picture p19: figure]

1

2
3

5

6

1: Run 6mm drill through x-rod holes in body (A) to ensure rods will fit.
2: Insert long 8mm linear bearing into body.
3: Use 2x 3mm locknuts and 2x 3x12mm screws to secure y-belt clip (B) to body. Don’t tighten down screws yet.
4: Insert 3mm locknut in x idler bracket (C).
5: Use 1x 3mm locknut and 1x 3x20mm SHCS to secure 14-tooth idler in bracket. Don’t over-tighten the screw; make sure the idler spins freely.
6: Use 1x 3x16mm SHCS to attach idler bracket to body. The head of the screw installed in step 5 should protrude through the oval slot in the body. Only insert the screw far enough to fully engage the locknut in the bracket; there should be a gap of ~5mm between bracket and outside of the body.

### XY Joiners assembly

A

### X Carriage initial assembly

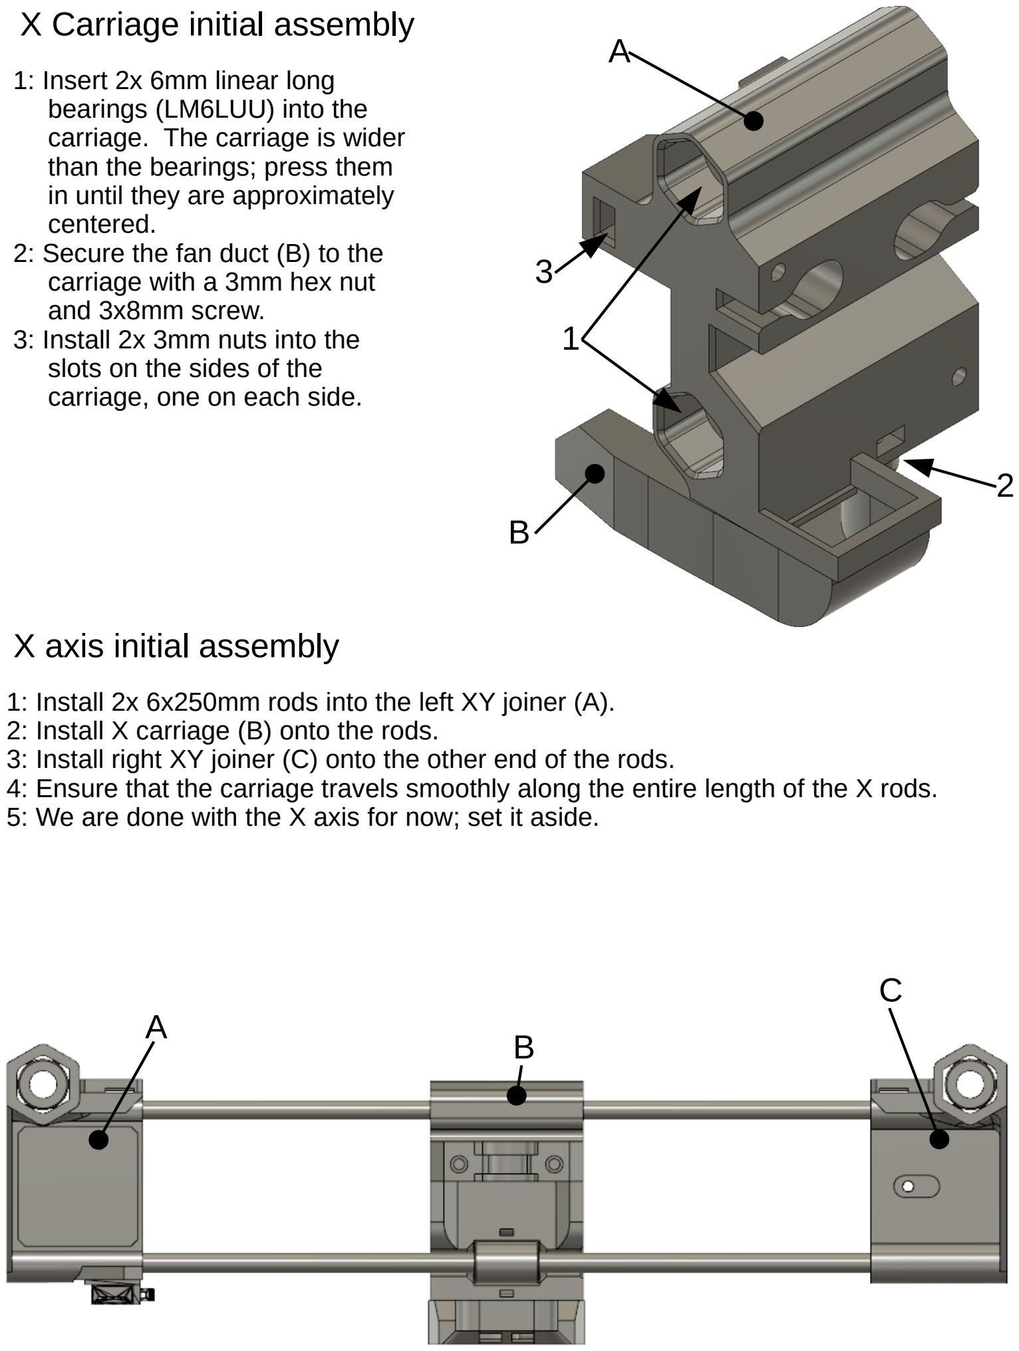
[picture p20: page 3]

1

2
B

1: Insert 2x 6mm linear long bearings (LM6LUU) into the carriage. The carriage is wider than the bearings; press them in until they are approximately centered.
2: Secure the fan duct (B) to the carriage with a 3mm hex nut and 3x8mm screw.
3: Install 2x 3mm nuts into the slots on the sides of the
carriage, one on each side.

1: Install 2x 6x250mm rods into the left XY joiner (A).
2: Install X carriage (B) onto the rods.
3: Install right XY joiner (C) onto the other end of the rods.
4: Ensure that the carriage travels smoothly along the entire length of the X rods. 5: We are done with the X axis for now; set it aside.

### X axis initial assembly

C
A
B

3

### Upper frame assembly

- Assemble the upper half of the printer frame from 2x Z extrusions (A – 304mm long, ends tappped), 2x X extrusions (B – 300mm long, ends tapped), 2x Y extrusions (C – 300mm long, ends cross-drilled), and 6x 5x14mm BHCS.
- To assemble the extrusions, insert a screw into the end of a tapped extrusion until ~3mm of thread is left showing. Then slide the screw head into one face of a cross-drilled extrusion, and insert a hex key through the cross-drilled hole to tighten the screw.
- As you assemble the frame, insert T-slot nuts as shown below. (T-slot nuts are inserted from the end of an extrusion; the ones noted below cannot be added after the frame is assembled because the ends of the extrusions will be blocked.) (6x

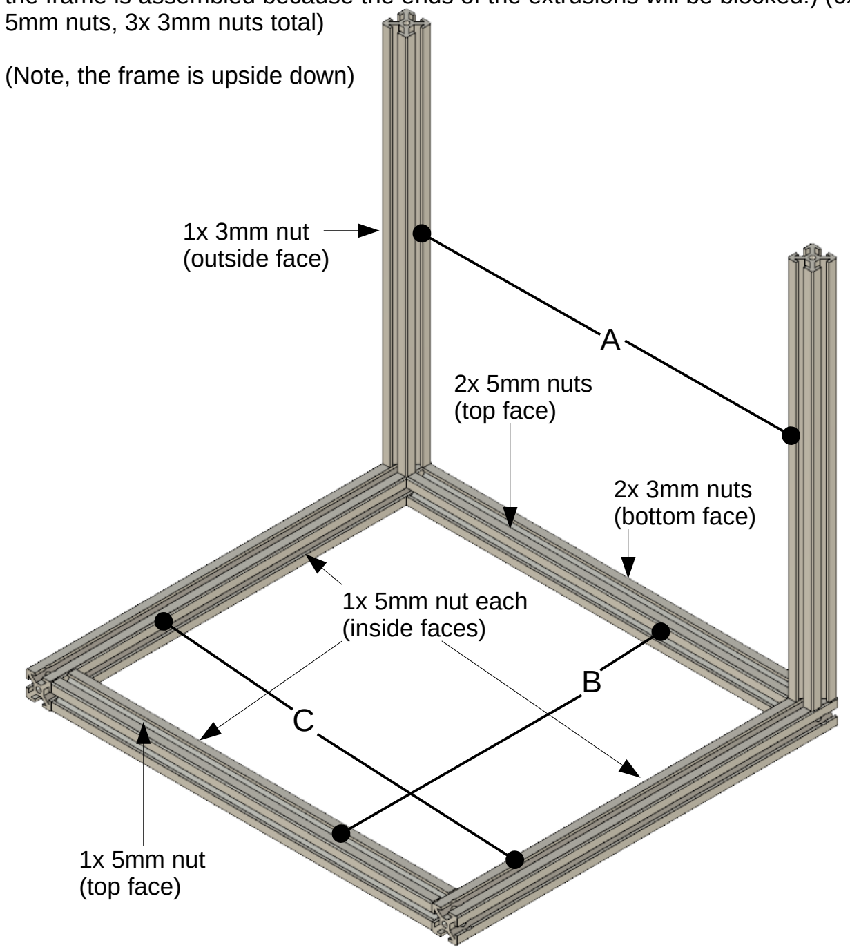
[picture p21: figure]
5mm nuts, 3x 3mm nuts total); (Note, the frame is upside down); 2x 5mm nuts (top face); 2x 3mm nuts (bottom face); 1x 5mm nut each (inside faces); 1x 5mm nut (top face); 1x 3mm nut (outside face)

### XY assembly 1

1: Install left and right-front Y anchors (B, C) onto front of the frame (A) using 4x 5x10mm screws and two more 5mm T-slot nuts. Tighten these screws until snug. Note that the screws pointed to in the figure below must be button heads; the others can be socket heads.
2: Insert 3x 3mm T-slot nuts in the top face of the left extrusion.
3: Insert 2x 3mm T-slot nuts in the top face of the right extrusion
4: Press 1x 6mm bearing into each of the left and right-rear Y anchors (D, E).
5: Install 3x 20-tooth pulleys on a 6x250mm rod (F). Note the orientation of the pulleys in the figure below. Notches ground into the rod should match the locations of the pulleys on the rod. Apply thread locker to the set screws in the pulleys and tighten them to lock the pulleys in place.
6: Place 2x 550mm belts and 1x 98mm belt around the rod assembly (F), insert the rod into the bearings of the rear anchors (D, E), and install the anchors onto the frame using 4x 5x10mm screws and 2 more 5mm T-slot nuts. Do not tighten these screws yet.
The rod should have ~1mm of play left-to-right between the anchors and should spin freely. If the pulleys are pressed into the anchors, loosen their set screws and nudge the pulleys in.

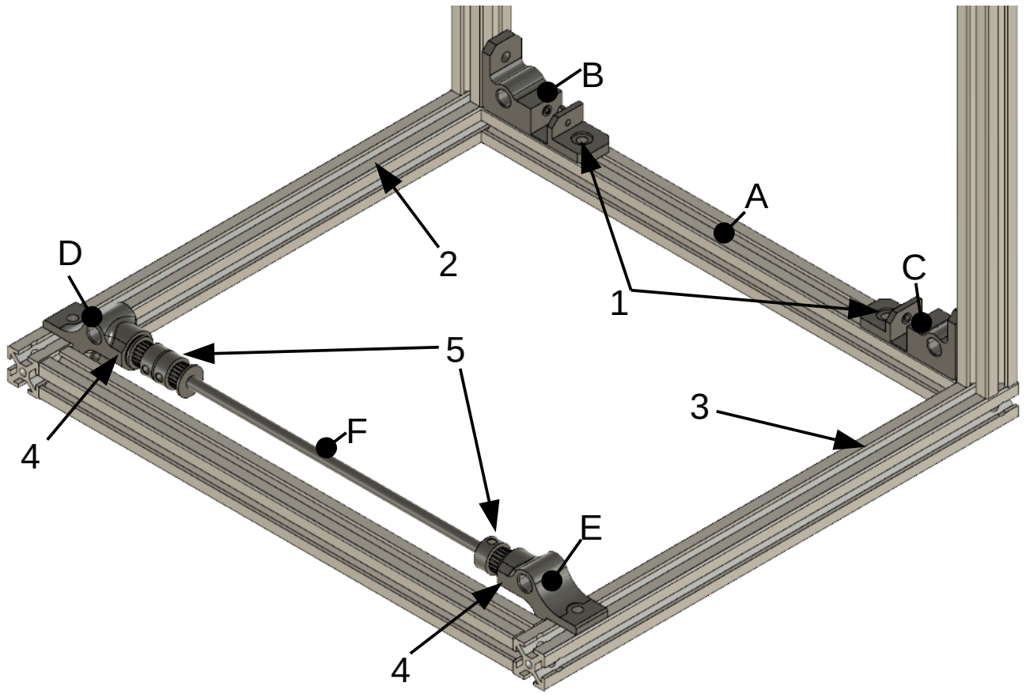
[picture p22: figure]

### XY Assembly 2

1: Insert 2x 8x300mm rods (A) into the front Y anchors (B). Push them in until about the same length of rod is sticking out in front of and behind the anchors.
2: Slip the X axis assembly (C) onto the Y rods. Make sure the assembly is oriented as shown in the figure.
3: Continue to push the Y rods back and feed them through the rear anchors (D). The front of the Y rods should be flush with the front of the front anchors; about 20mm of rod will stick out the back of the rear anchors.
4: Install the Y-axis stepper motor (F) on its bracket (E) using 4x 3x10mm screws. Don’t tighten down these screws yet.
5: Install a 14-tooth pulley onto the stepper motor (F).
6: Install the Y-axis motor assembly onto the rear extrusion of the frame using 2x 5x10 screws. Align the pulley on the motor with the middle pulley on the Y-axis axle, then tighten these screws until snug.
7: Loop one of the 550mm belts around a 14-tooth idler then insert the idler in the front Y anchor. Secure the idler with a 3x20mm SHCS. Insert the screw until the head is seated, but do not clamp the idler; make sure the idler can still spin freely. You may need to temporarily remove the adjacent 5x10 BHCS to install this screw. Repeat for the other 550mm belt and other front Y anchor.
8: Ensure the 550mm belts are seated on the pulleys on the Y axle and run under the belt clips on the XY joiners, then push the rear anchors (D) back until the Y belts are tensioned. Each belt should vibrate like a low-pitched guitar string. Tighten down the mounting screws for the rear Y anchors until snug.
9: Slip the 98mm belt around the middle pulley on the Y axle and the pulley on the Y motor, then tighten the Y motor screws while pulling up on the motor to tension the

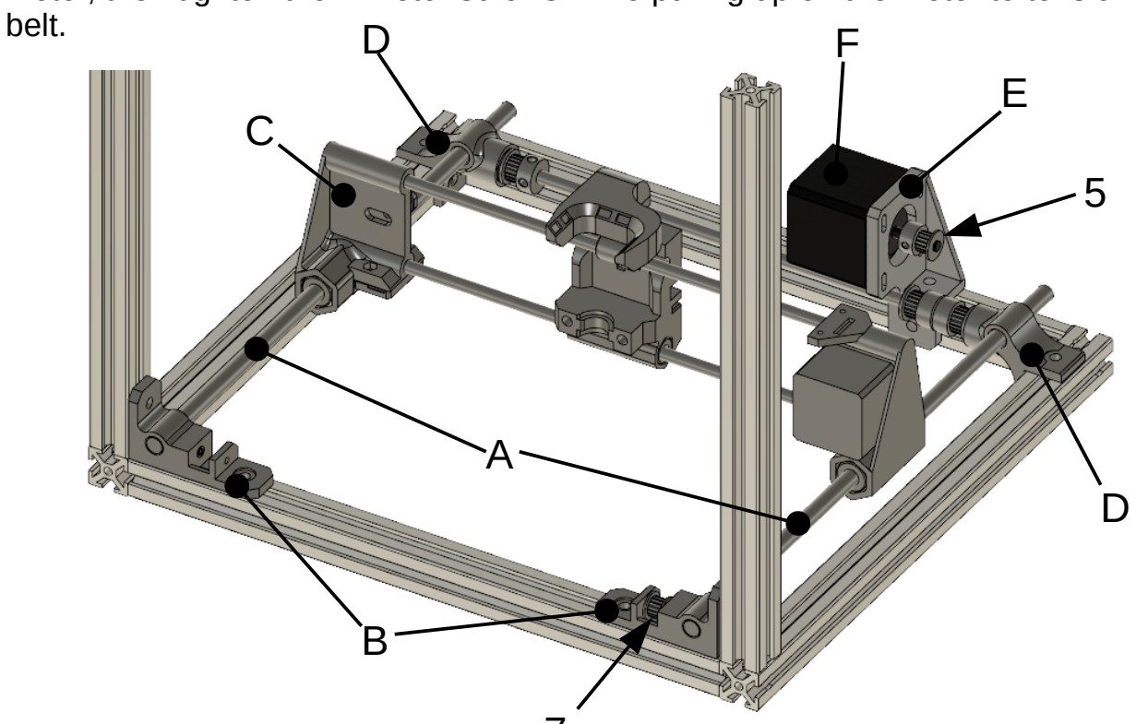
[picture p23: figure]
belt.

7

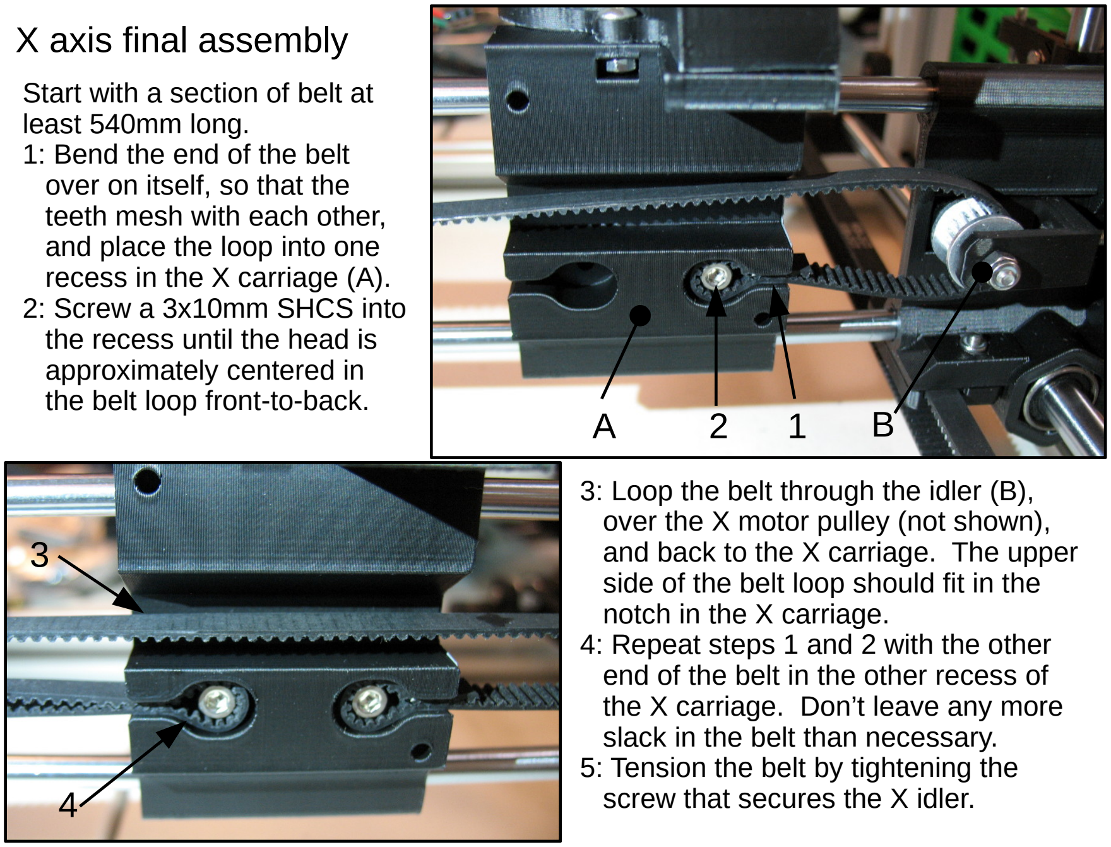
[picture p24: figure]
X axis final assembly; Start with a section of belt at least 540mm long. 1: Bend the end of the belt over on itself, so that the teeth mesh with each other, and place the loop into one recess in the X carriage (A). 2: Screw a 3x10mm SHCS into the recess until the head is approximately centered in the belt loop front-to-back.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
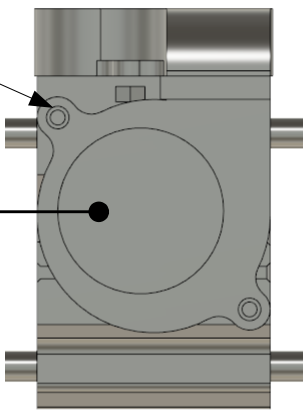
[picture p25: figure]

C

7

6: Adjust the pulley on the X motor so that it is aligned with the belt anchor on the X carriage and the X idler, and the upper side of the belt is centered front-to-back in the notch in the carriage. (Not shown.)
7: Install the part cooling blower (C) onto the X carriage with 2x 3x16mm screws. These screws are threading into soft plastic. Tighten them just enough to keep the fan from moving; overtightening will strip the threads in the plastic.

### XY final assembly

1: Install an endstop switch on the Y axis endstop holder (A) with 2x 2x8 mm wood screws.
2: Install the Y endstop assembly on the frame with a 3x10mm screw and the rear-most T-slot nut. Slide the endstop assembly all the way back until it contacts the rear Y anchor, then tighten the screw until snug.
3: Install the RAMPS case base (B) on the frame with 3x 3mm T-slot nuts and 3x 3x10mm screws. If using different electronics, install the appropriate base at this time. (If the electronics case has already been assembled, install the entire assembly at this time.)

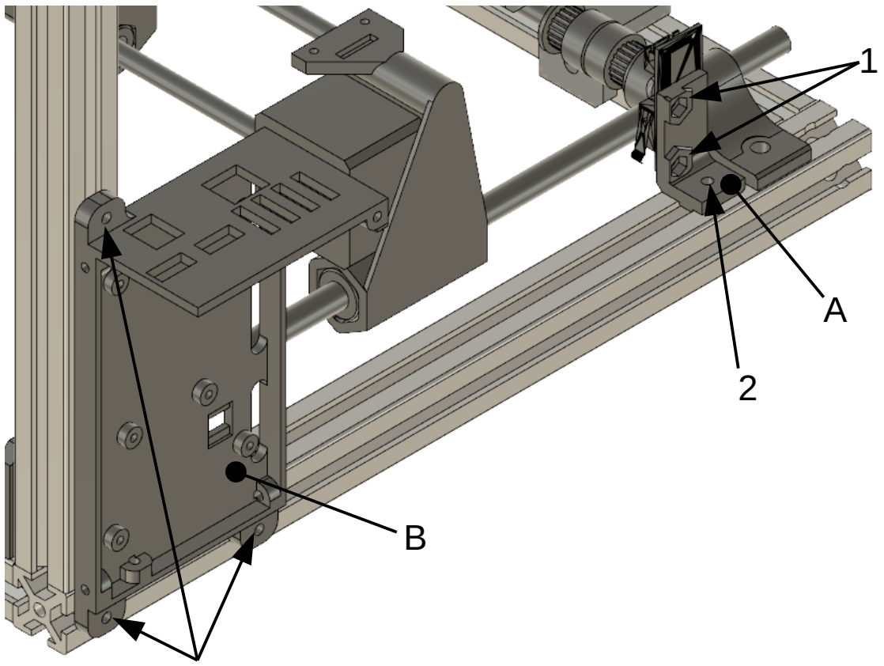
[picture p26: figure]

3

### Lower frame assembly

- Assemble the lower half of the printer frame from 2x Z extrusions (A – 304mm long, ends tappped), 2x X extrusions (B – 300mm long, ends tapped), 2x Y extrusions (C – 300mm long, ends cross-drilled), and 6x 5x14mm BHCS.
- As you assemble the frame, insert T-slot nuts as shown below. (These nuts are installed from the end of an extrusion; the ones noted below cannot be added after the frame is assembled because the ends of the extrusions will be blocked.) (4x 5mm nuts total)
- The two nuts at the back of the frame are for the 12V power supply. If not using a Meanwell LRS-350-12 type power supply, you may need T-slot nuts in different locations for a different set of power supply mounts.

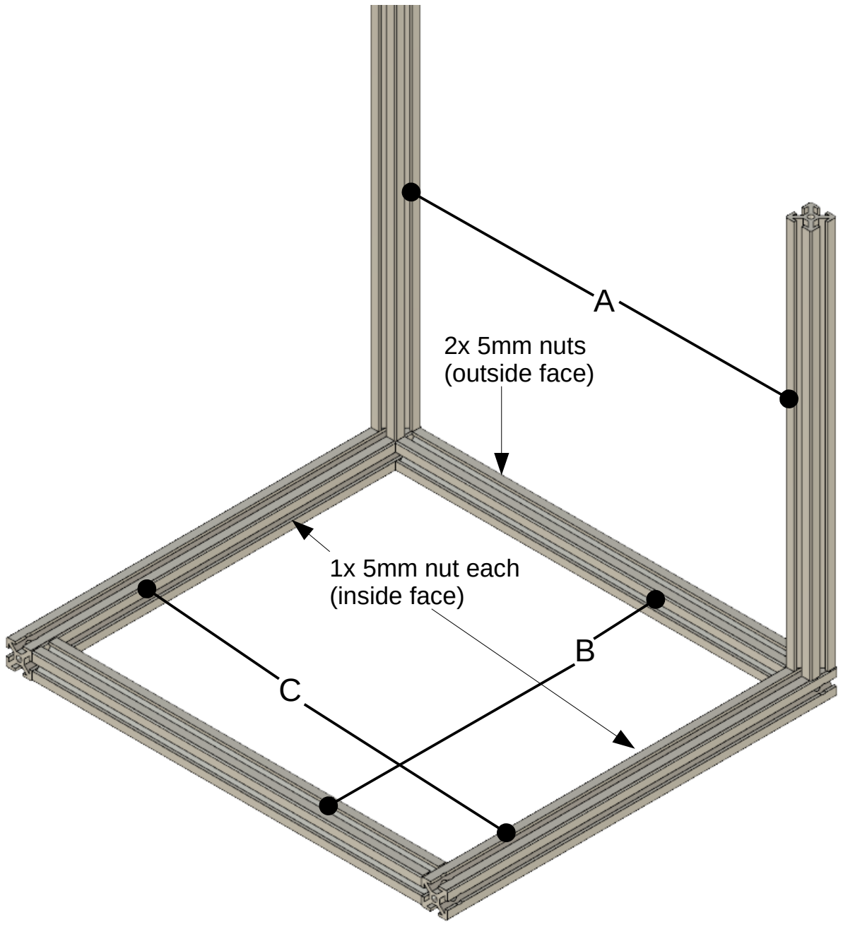
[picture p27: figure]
2x 5mm nuts (outside face); 1x 5mm nut each (inside face)

### Z axis assembly 1

1: Using 4x 3x8mm screws, install Z axis motor (A) onto Z motor bracket (B).
2: Install a 20-tooth pulley on the Z axis motor – make sure this pulley has a 5mm bore; it should fit snugly on the motor axle.
3: Install Z motor assembly onto frame using 2x 5mm T-slot nuts and 2x 5x10mm screws. Slide the motor towards the back of the frame but do not tighten these screws yet.
4: Press a 6mm bearing into a Z axis base block (C).
5: Install the base block assembly on the frame using 1x 5x10mm screw (using the front hole on the side of the base block), 2x 3mm T-slot nuts, and 2x 3x10mm screws. Do not tighten these screws yet.
6: Place the shorter Z axis spacer (D) against the inside of the frame in front of the base assembly.
7: Slide the base assembly forwards against the spacer and tighten its screws until snug.
8: Remove the spacer, then repeat steps 4-7 with the other Z base on the other side of the frame (not shown).
9: Install 4x feet on the bottom of the frame (not shown).

A

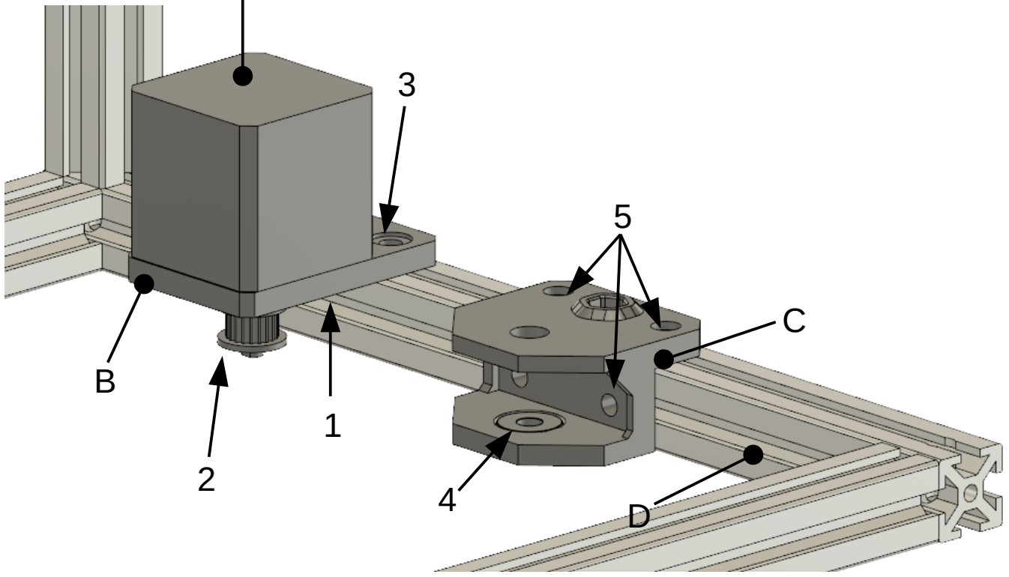
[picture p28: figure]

### Z axis assembly 2

1: Place a washer on the 6mm bearing in the Z base block.
2: Wrap the 700mm belt around a 20-tooth pulley and hold the pulley in place above the bearing and washer. Placing the pulley without dislodging the washer is tricky; you can use a skinny tool such as a small screwdriver to reach down through the bore of the pulley and nudge the washer back into position.
3: Insert a 6x250mm leadscrew down through the base block, pulley, washer, and bearing. One side of the leadscrew has a notch ground in it; that notch should line up with a set screw in the pulley. About 3mm of the leadscrew will protrude from the bottom of the bearing when it is properly aligned.
4: Apply thread locker to the set screws in the pulley and tighten them down to secure the rod in place.
5: Repeat steps 1-4 with the other Z base assembly. (The same 700mm belt should be wrapped around the other pulley; make sure the belt is not twisted or tangled.) 6: Thread one leadscrew nut on each leadscrew, with the flange on the bottom. (Not shown.)

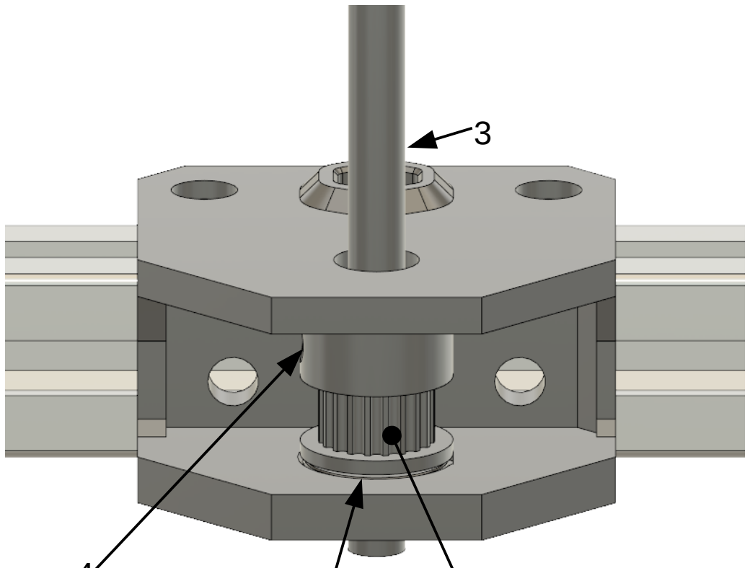
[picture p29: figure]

1 2

4

### Bed assembly

1: Press a bearing block bottom half (A) and top half (B) together with a long 8mm linear bearing. Repeat to make two bearing block assemblies.
2: Install 2x 3mm lock nuts into each of the bearing block assemblies (4 total).
3: Install 2x bed extrusions (C, 300mm length, not threaded or cross-drilled) onto the lefthand bearing block assembly with 2x 5mm T-slot nuts and 2x 5x10mm screws. 4: Slide 2x 3mm T-slot nuts into the top side of each bed extrusion (4 total).
5: Install the righthand bearing block assembly and Z endstop bracket (D) with 2x 5mm T-slot nuts, 1x 5x10mm screw, and 1x 5x14mm screw.
6: Install endstop on the bracket with 2x wood screws. Don’t over-tighten these screws.
7: Install heatbed (E) with 4x 3x20mm screws, 4x springs, 4x washers, and the T-slot nuts installed in step 4. The heatbed’s connector should be on the lefthand side. From top to bottom, each screw goes through the heatbed, spring, washer, then nut. If the springs are particularly short, you may also need to install spacers.
8: One screw at a time, remove each heatbed screw and apply thread locker to it, then reinstall the screw and tighten it until its end bottoms out on the extrusion, then back the screw off 1mm (2 complete rotations).

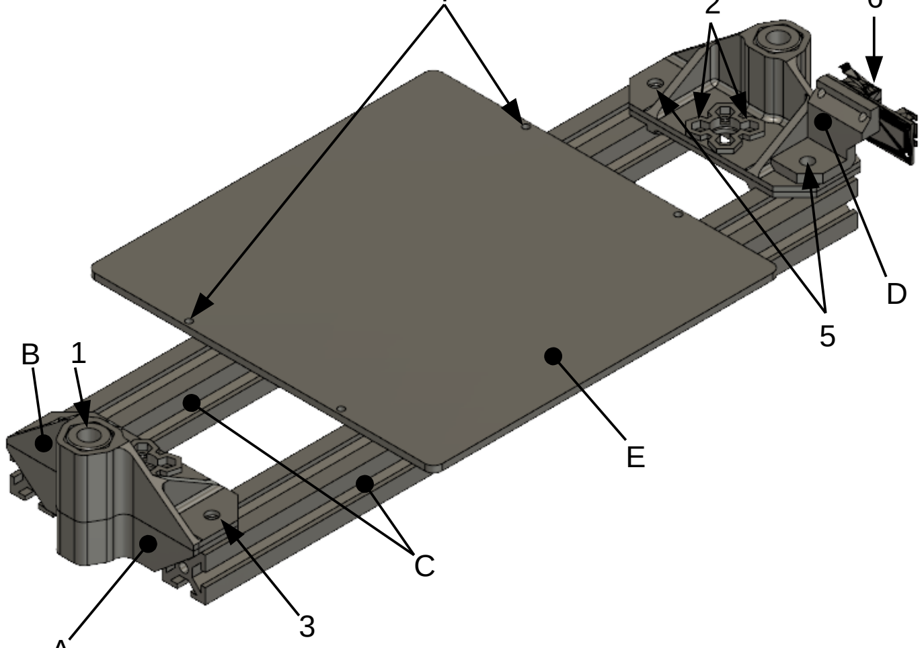
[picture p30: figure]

A

2

6

7

### Z axis assembly 3

1: Install a 8x300mm rod in each Z base.
2: Install the bed assembly onto the Z rods.
3: Slide the Z endstop onto the righthand Z rod. Install a 3x16mm SHCS on the end of the endstop, with the head of the screw on the bottom and about 5mm of thread between the screw head and endstop. Install a 3mm hex nut and 3x10mm screw in the endstop to secure it in place. Don’t tighten this screw yet.
4: Place a Z axis top anchor (D) on the top of each Z rod.
5: Spin the leadscrew nuts down near to the bottom of the leadscrews so that the bed sits near the bottom of the printer.

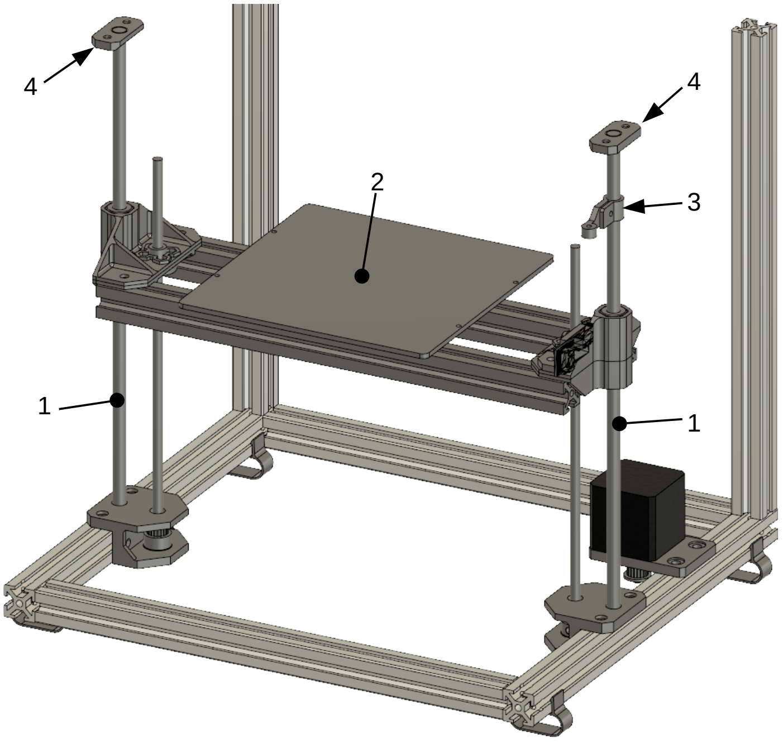
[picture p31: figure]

### Power supply assembly

1: Wire together the power inlet (not shown), snap it into the power supply case (A), and wire it to the input terminals of the power supply (not shown). If you are not 100% comfortable with this step, get someone to help you. Mains wiring is hazardous!
2: Attach the power supply case to the power supply (B) with 2x 4x8mm screws.
3: Attach the bottom cover to the case with 2x 3x8mm screws (not shown).
4: Attach the power supply bracket (C) to the power supply with 1x 4x8mm screw and 1x 4x5mm screw.
5: Mount the power supply to the frame with one more 5mm T-slot nut and 3x 5x10 screws.
(Leave the top cover off of the power supply case until the 12V wiring is done.)

### 1 (power inlet goes here)

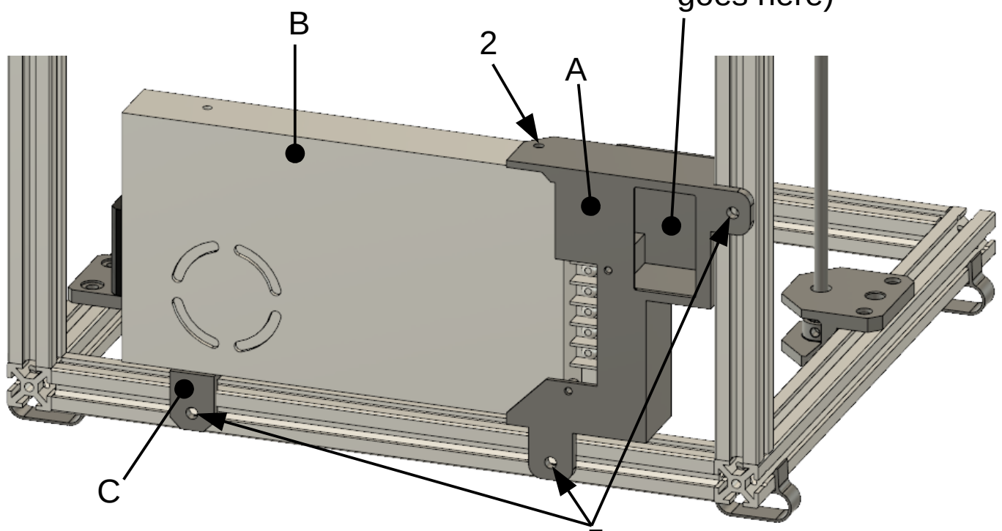
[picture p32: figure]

5

### Frame final assembly

1: Assemble the top and bottom frame halves. Insert 4x 5x14mm BHCS in the unconnected ends of the Z extrusions, then slide the top half of the frame onto the bottom half. Tighten down the screws, and take this opportunity to ensure all of the other screws fastening the frame together are tight.
2: Use 4x 3x10mm screws to fasten the Z axis top anchors to the top frame. Use the longer Z axis spacer to ensure the anchors are the correct distance from the front of the frame. If you have trouble getting the anchors to line up left-to-right, loosen the two 5mm bolts that attach the left Z bearing block to the bed extrusions.

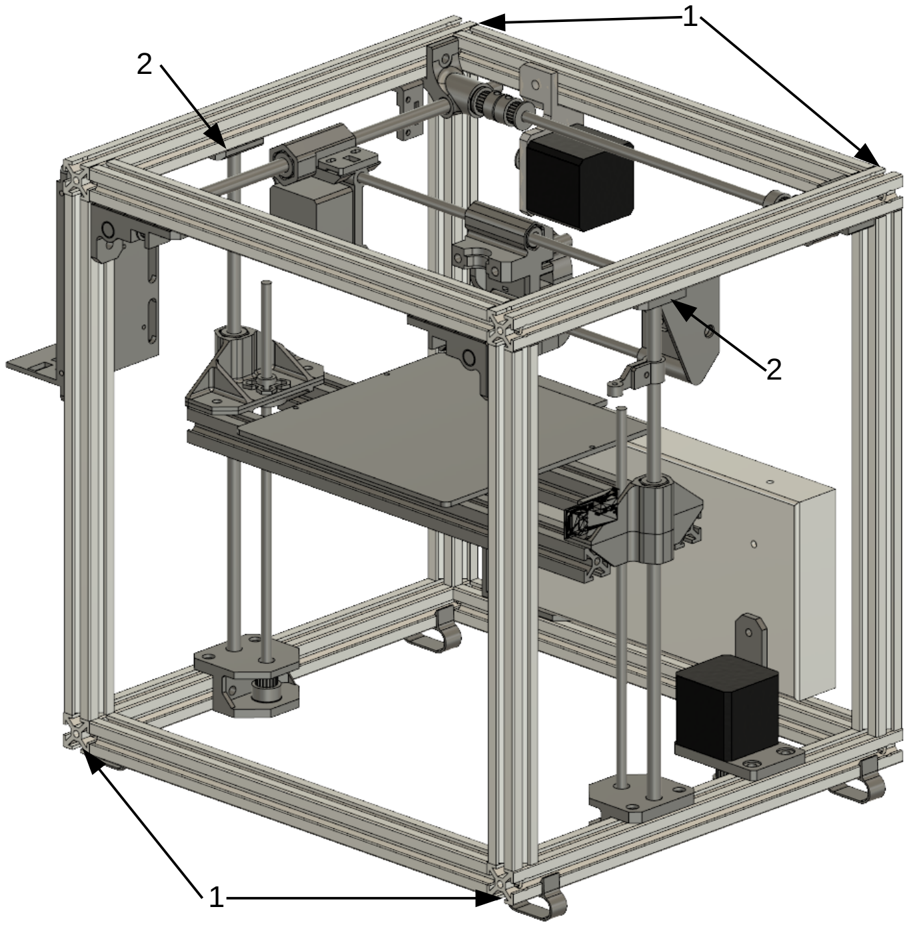
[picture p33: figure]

### Z axis final assembly

1: Re-tighten the 5mm screws in the bed assembly, if needed. Ensure that the bed assembly slides smoothly over the whole length of the Z rods.
2: Tension the Z axis belt – ensure that the 700mm belt for the Z axis is seated on both pulleys on the leadscrews and the pulley on the Z axis motor, then tighten the screws on the Z motor assembly while pushing back on the assembly. Tension on this belt is important to ensure that the leadscrews always rotate together. If one rotates while the belt skips on the other, the bed can become skewed and, in extreme cases, bend or damage part of the Z assembly.
3: Check that the height of the pulley on the motor is correct; loosen its set screws and adjust if needed.
4: Hold the bed assembly up and spin both leadscrew nuts upwards a few inches, then let the bed rest on the nuts.
5: Fasten one leadscrew nut to its bearing block assembly with 2x 3x12mm screws. 6: Rotate the other leadscrew to adjust the angle of the bed until it is level with respect to the printer’s frame, then fasten it to its bearing block assembly as well.

### Last assembly steps

1: Secure a E3D V6-style hotend to the X carriage with the hotend clamp and 2x 3x20mm screws. Hotend wires should run up the left side of the X carriage; secure wires to the post on the hotend clamp with a ziptie if necessary.
2: Install an extruder to the left side of the frame just behind the electronics with appropriate hardware.
3: Install the filament hook at the left-rear corner of the frame with a 5mm T-slot nut and 5x10mm screw.
4: Cut Bowden tube to correct length and install between extruder and hotend.
5: Screw Arduino to the RAMPS case base with 6x 2.5x6mm SHCS if not already done.
6: Install RAMPS board, stepper drivers, and display adapter, if not already done. 7: Attach RAMPS case lid with 4x 3x8mm screws.

### Cable routing 1

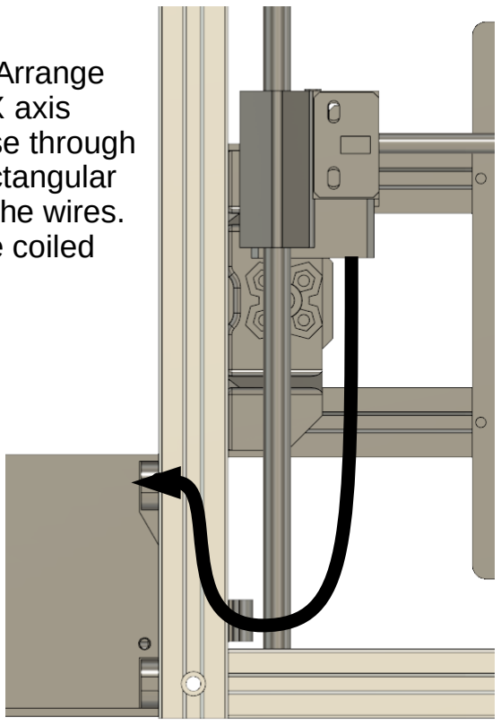
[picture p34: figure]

Bundle the X motor and X endstop wires together. Arrange them so that they come straight forwards from the X axis assembly, then turn back and enter the RAMPS case through the uppermost hole in its base. There is a small rectangular slot in the base for attaching a cable clip to secure the wires. The excess length of the X endstop wires should be coiled up and secured inside the RAMPS case.
The bed heater wires should be secured to the
front bed extrusion, then routed down to the front-left corner of the printer frame and up to the appropriate terminals in the end of the RAMPS case.
The Z endstop and bed thermistor wires can be bundled together with the heater wires or, if they aren’t long enough for that, they can be routed up along the front-left Z extrusion and into the
RAMPS case through its base. Leave a loop of wire under the bed so there is sufficient slack when the bed moves to the bottom of the printer.

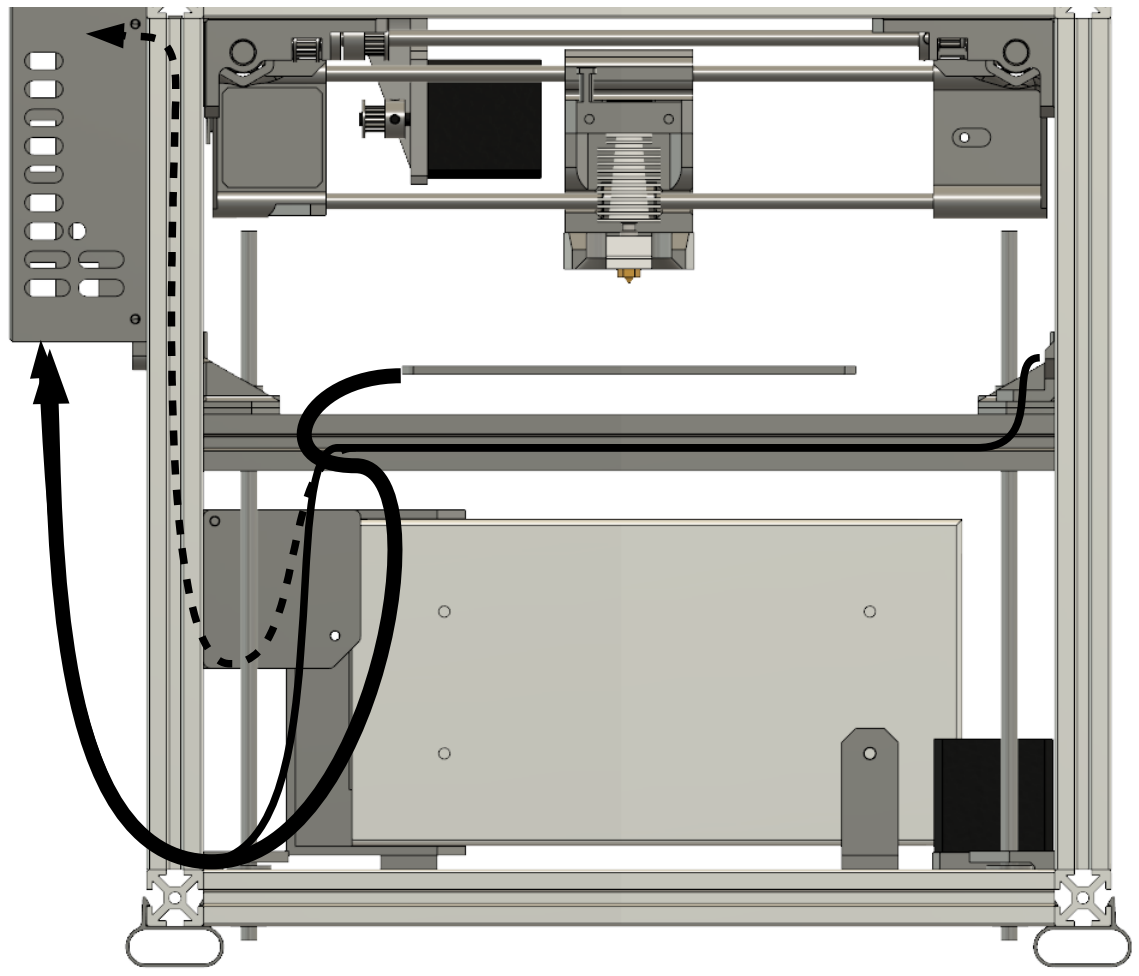
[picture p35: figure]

### Cable routing 2

Other wires in the printer should be routed to the bottom-left corner of the frame, then forwards and up to the RAMPS case. This includes the Z motor wires (route along the rear-bottom X extrusion), Y motor and endstop wires (bundle together at the top-left-rear corner then route down to the corner), and power supply wires.

After connecting the power supply wires to the 12V terminals of the power supply, fasten the power supply case top cover to the case with 2x 3x8mm screws (not shown).

Wires from the X carriage (not shown) should be bundled along the Bowden tube to the extruder, then routed into the RAMPS case.

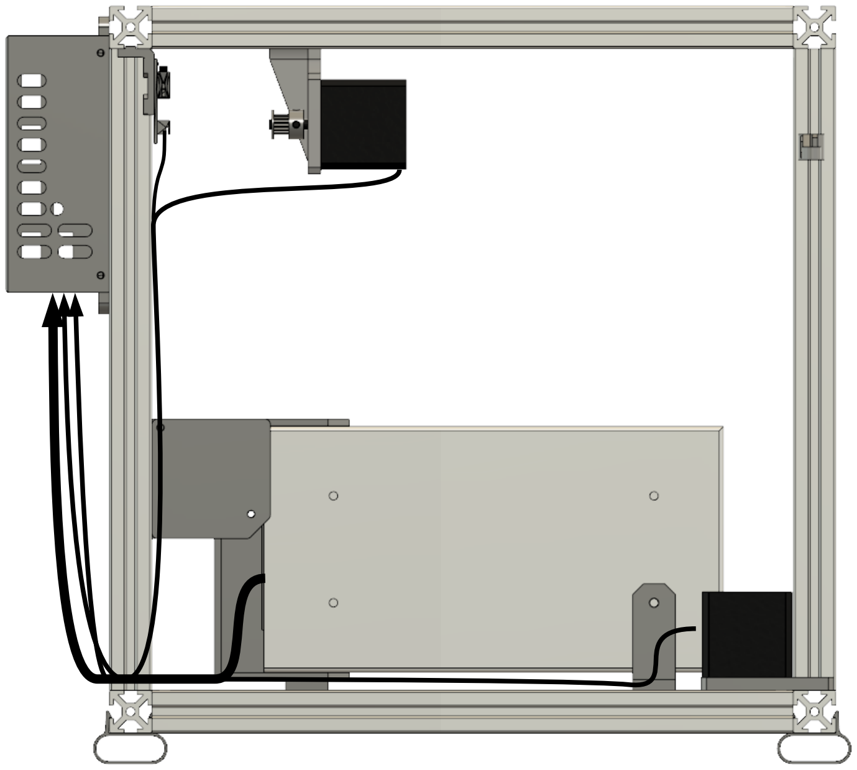
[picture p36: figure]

### Bed leveling

1: Move the bed upwards until it is very close to touching the hotend nozzle (~1mm gap).
2: Move the Z endstop down the Z rod until the head of the screw on the endstop just triggers the Z endstop switch.
3: Tighten the screw on the Z endstop to fix its position. Fine adjustment of the level of the bed will be done by rotating the vertical screw in the endstop.
4: Now the bed can be leveled using the paper gap method, which unfortunately is a bit too involved to describe here. Look online for guides to this leveling method.

You should now be ready to try out the printer!

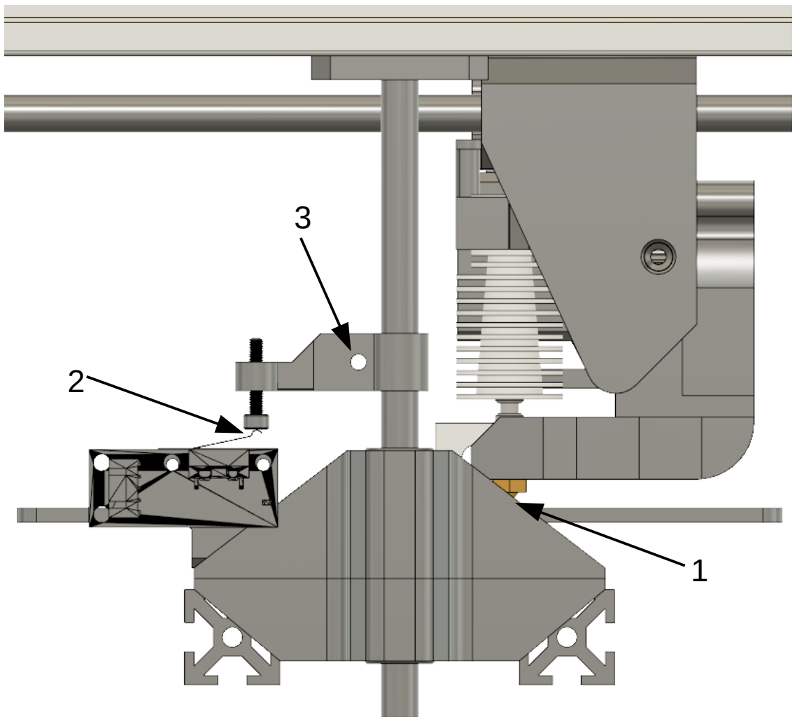
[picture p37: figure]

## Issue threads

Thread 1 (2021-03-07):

Extruder/feeder motor constantly/randomly retracting

mathlete2630, 2021-03-07:
Hi, my name is Aadit and I was part of this camp in the summer of 2019. My extruder motor is just constantly retracting while printing. I have checked all my settings. The retraction is 2mm, the filament size is correct; I am using PLA; and everything else is also correct. If I could get help with this, that would be great. Thanks!

I have also attached a video that shows what is happening.

https://user-images.githubusercontent.com/65245538/110254031-9213a300-7f4a-11eb-8ed5-641df507afbd.mp4

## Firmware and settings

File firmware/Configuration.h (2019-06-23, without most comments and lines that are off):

#define CONFIGURATION_H
#define CONFIGURATION_H_VERSION 010109
#define STRING_CONFIG_H_AUTHOR "Matt Roesle, Hypatia Studio LLC" // Who made the changes.
#define SHOW_BOOTSCREEN
#define STRING_SPLASH_LINE1 SHORT_BUILD_VERSION // will be shown during bootup in line 1
#define STRING_SPLASH_LINE2 WEBSITE_URL         // will be shown during bootup in line 2
#define SERIAL_PORT 0
#define BAUDRATE 115200
  #define MOTHERBOARD BOARD_RAMPS_14_EFB
#define CUSTOM_MACHINE_NAME "My Summer Printer"
#define EXTRUDERS 1
#define DEFAULT_NOMINAL_FILAMENT_DIA 1.75
#define POWER_SUPPLY 0
#define TEMP_SENSOR_0 5
#define TEMP_SENSOR_1 0
#define TEMP_SENSOR_2 0
#define TEMP_SENSOR_3 0
#define TEMP_SENSOR_4 0
#define TEMP_SENSOR_BED 11
#define TEMP_SENSOR_CHAMBER 0
#define DUMMY_THERMISTOR_998_VALUE 25
#define DUMMY_THERMISTOR_999_VALUE 100
#define MAX_REDUNDANT_TEMP_SENSOR_DIFF 10
#define TEMP_RESIDENCY_TIME 10  // (seconds)
#define TEMP_HYSTERESIS 3       // (degC) range of +/- temperatures considered "close" to the target one
#define TEMP_WINDOW     1       // (degC) Window around target to start the residency timer x degC early.
#define TEMP_BED_RESIDENCY_TIME 10  // (seconds)
#define TEMP_BED_HYSTERESIS 3       // (degC) range of +/- temperatures considered "close" to the target one
#define TEMP_BED_WINDOW     1       // (degC) Window around target to start the residency timer x degC early.
#define HEATER_0_MINTEMP 10
#define HEATER_1_MINTEMP 5
#define HEATER_2_MINTEMP 5
#define HEATER_3_MINTEMP 5
#define HEATER_4_MINTEMP 5
#define BED_MINTEMP 10
#define HEATER_0_MAXTEMP 265
#define HEATER_1_MAXTEMP 275
#define HEATER_2_MAXTEMP 275
#define HEATER_3_MAXTEMP 275
#define HEATER_4_MAXTEMP 275
#define BED_MAXTEMP 120
#define PIDTEMP
#define BANG_MAX 255     // Limits current to nozzle while in bang-bang mode; 255=full current
#define PID_MAX BANG_MAX // Limits current to nozzle while PID is active (see PID_FUNCTIONAL_RANGE below); 255=full current
#define PID_K1 0.95      // Smoothing factor within any PID loop
  #define PID_FUNCTIONAL_RANGE 10 // If the temperature difference between the target temperature and the actual temperature
#define DEFAULT_Kp 11.52
#define DEFAULT_Ki 0.62
#define DEFAULT_Kd 53.34
#define PIDTEMPBED
#define MAX_BED_POWER 255 // limits duty cycle to bed; 255=full current
#define DEFAULT_bedKp 158.45
#define DEFAULT_bedKi 30.70
#define DEFAULT_bedKd 204.44
#define EXTRUDE_MINTEMP 170
#define PREVENT_LENGTHY_EXTRUDE
#define EXTRUDE_MAXLENGTH 500
#define THERMAL_PROTECTION_HOTENDS // Enable thermal protection for all extruders
#define THERMAL_PROTECTION_BED     // Enable thermal protection for the heated bed
#define USE_XMIN_PLUG
#define USE_ZMIN_PLUG
#define USE_YMAX_PLUG
#define ENDSTOPPULLUPS
#define X_MIN_ENDSTOP_INVERTING true // set to true to invert the logic of the endstop.
#define Y_MIN_ENDSTOP_INVERTING false // set to true to invert the logic of the endstop.
#define Z_MIN_ENDSTOP_INVERTING true // set to true to invert the logic of the endstop.
#define X_MAX_ENDSTOP_INVERTING false // set to true to invert the logic of the endstop.
#define Y_MAX_ENDSTOP_INVERTING true // set to true to invert the logic of the endstop.
#define Z_MAX_ENDSTOP_INVERTING false // set to true to invert the logic of the endstop.
#define Z_MIN_PROBE_ENDSTOP_INVERTING false // set to true to invert the logic of the probe.
#define X_DRIVER_TYPE  A4988
#define Y_DRIVER_TYPE  A4988
#define Z_DRIVER_TYPE  A4988
#define E0_DRIVER_TYPE A4988
#define DEFAULT_AXIS_STEPS_PER_UNIT   { 100, 100, 1600, 100.2 }
#define DEFAULT_MAX_FEEDRATE          { 300, 300, 20, 75 }
#define DEFAULT_MAX_ACCELERATION      { 3000, 3000, 200, 10000 }
#define DEFAULT_ACCELERATION          2500    // X, Y, Z and E acceleration for printing moves
#define DEFAULT_RETRACT_ACCELERATION  10000    // E acceleration for retracts
#define DEFAULT_TRAVEL_ACCELERATION   2500    // X, Y, Z acceleration for travel (non printing) moves
#define DEFAULT_XJERK                 3.0
#define DEFAULT_YJERK                 3.0
#define DEFAULT_ZJERK                  0.3
#define DEFAULT_EJERK                  5.0
#define Z_MIN_PROBE_USES_Z_MIN_ENDSTOP_PIN
#define X_PROBE_OFFSET_FROM_EXTRUDER 10  // X offset: -left  +right  [of the nozzle]
#define Y_PROBE_OFFSET_FROM_EXTRUDER 10  // Y offset: -front +behind [the nozzle]
#define Z_PROBE_OFFSET_FROM_EXTRUDER 0   // Z offset: -below +above  [the nozzle]
#define MIN_PROBE_EDGE 10
#define XY_PROBE_SPEED 8000
#define Z_PROBE_SPEED_FAST HOMING_FEEDRATE_Z
#define Z_PROBE_SPEED_SLOW (Z_PROBE_SPEED_FAST / 2)
#define Z_CLEARANCE_DEPLOY_PROBE   10 // Z Clearance for Deploy/Stow
#define Z_CLEARANCE_BETWEEN_PROBES  5 // Z Clearance between probe points
#define Z_CLEARANCE_MULTI_PROBE     5 // Z Clearance between multiple probes
#define Z_PROBE_LOW_POINT          -2 // Farthest distance below the trigger-point to go before stopping
#define Z_PROBE_OFFSET_RANGE_MIN -20
#define Z_PROBE_OFFSET_RANGE_MAX 20
#define X_ENABLE_ON 0
#define Y_ENABLE_ON 0
#define Z_ENABLE_ON 0
#define E_ENABLE_ON 0 // For all extruders
#define DISABLE_X false
#define DISABLE_Y false
#define DISABLE_Z false
#define DISABLE_E false // For all extruders
#define DISABLE_INACTIVE_EXTRUDER true // Keep only the active extruder enabled.
#define INVERT_X_DIR true
#define INVERT_Y_DIR false
#define INVERT_Z_DIR false
#define INVERT_E0_DIR false
#define INVERT_E1_DIR false
#define INVERT_E2_DIR false
#define INVERT_E3_DIR false
#define INVERT_E4_DIR false
#define X_HOME_DIR -1
#define Y_HOME_DIR 1
#define Z_HOME_DIR -1
#define X_BED_SIZE 160
#define Y_BED_SIZE 160
#define X_MIN_POS 0
#define Y_MIN_POS 0
#define Z_MIN_POS 0
#define X_MAX_POS X_BED_SIZE
#define Y_MAX_POS Y_BED_SIZE
#define Z_MAX_POS 160
#define MIN_SOFTWARE_ENDSTOPS
  #define MIN_SOFTWARE_ENDSTOP_X
  #define MIN_SOFTWARE_ENDSTOP_Y
  #define MIN_SOFTWARE_ENDSTOP_Z
#define MAX_SOFTWARE_ENDSTOPS
  #define MAX_SOFTWARE_ENDSTOP_X
  #define MAX_SOFTWARE_ENDSTOP_Y
  #define MAX_SOFTWARE_ENDSTOP_Z
#define HOMING_FEEDRATE_XY (50*60)
#define HOMING_FEEDRATE_Z  (4*60)
#define EEPROM_SETTINGS // Enable for M500 and M501 commands
#define EEPROM_CHITCHAT   // Give feedback on EEPROM commands. Disable to save PROGMEM.
#define HOST_KEEPALIVE_FEATURE        // Disable this if your host doesn't like keepalive messages
#define DEFAULT_KEEPALIVE_INTERVAL 2  // Number of seconds between "busy" messages. Set with M113.
#define BUSY_WHILE_HEATING            // Some hosts require "busy" messages even during heating
#define PREHEAT_1_TEMP_HOTEND 200
#define PREHEAT_1_TEMP_BED     50
#define PREHEAT_1_FAN_SPEED     0 // Value from 0 to 255
#define PREHEAT_2_TEMP_HOTEND 240
#define PREHEAT_2_TEMP_BED    105
#define PREHEAT_2_FAN_SPEED     0 // Value from 0 to 255
#define PRINTJOB_TIMER_AUTOSTART
#define PRINTCOUNTER
#define LCD_LANGUAGE en
#define DISPLAY_CHARSET_HD44780 JAPANESE
#define SDSUPPORT
#define SPI_SPEED SPI_QUARTER_SPEED
#define REVERSE_ENCODER_DIRECTION
#define INDIVIDUAL_AXIS_HOMING_MENU
#define SPEAKER
#define LCD_FEEDBACK_FREQUENCY_DURATION_MS 70
#define LCD_FEEDBACK_FREQUENCY_HZ 2000
#define REPRAP_DISCOUNT_FULL_GRAPHIC_SMART_CONTROLLER
#define SOFT_PWM_SCALE 0
#define SERVO_DELAY { 300 }

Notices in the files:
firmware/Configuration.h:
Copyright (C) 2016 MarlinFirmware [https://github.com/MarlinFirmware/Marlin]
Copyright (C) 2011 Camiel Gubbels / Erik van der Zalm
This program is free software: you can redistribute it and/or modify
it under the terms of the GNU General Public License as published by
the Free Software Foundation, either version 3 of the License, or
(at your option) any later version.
